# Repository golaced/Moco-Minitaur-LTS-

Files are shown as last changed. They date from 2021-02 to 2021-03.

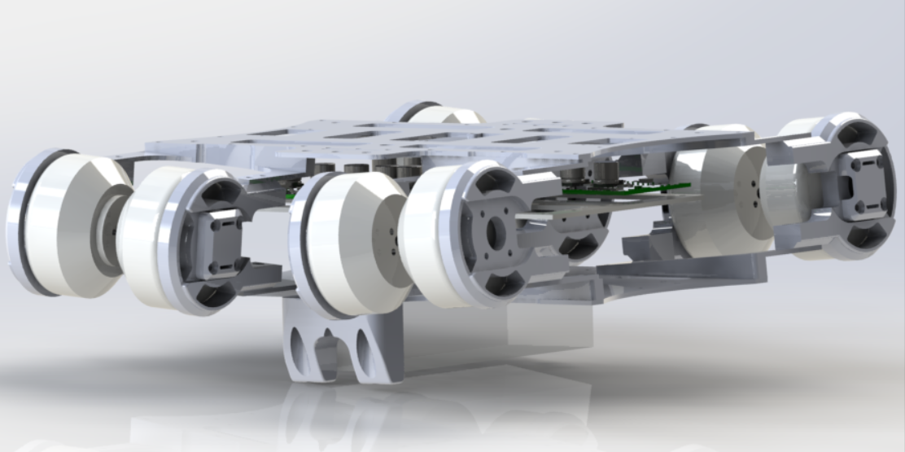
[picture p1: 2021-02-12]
教程4资料 机架设计/V2加工文件/渲染.PNG

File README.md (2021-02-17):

# Moco-Minitaur LTS 高性能 开源 力控 四足机器人 平台


本项目为开源桌面级8自由度四足机器人的相关资料，知乎教程文档：https://www.zhihu.com/column/c_1090923972006240256 </div><br>

教程1：Moco-ML项目介绍https://zhuanlan.zhihu.com/p/347235537</div><br>
教程2：机器人软硬件框架设计https://zhuanlan.zhihu.com/p/348091039</div><br>
教程3：电机驱动单元选https://zhuanlan.zhihu.com/p/349581111</div><br>
教程4：机器人主机架设计https://zhuanlan.zhihu.com/p/350553319</div><br>
教程5: ODrive驱动器改装https://zhuanlan.zhihu.com/p/351046678</div><br>
教程6：主控器设计和说明https://zhuanlan.zhihu.com/p/351052766</div><br>

官方taobao链接：https://item.taobao.com/item.htm?spm=a1z10.1-c.w4004-15110596499.22.6b86242c3mvjW9&id=589551490320
<br>
**-如果该项目对您有帮助请 Star 我们的项目-**<br>
**-如果您愿意分享对该项目的优化和改进请联系golaced@163.com或加入我们的QQ群567423074，加速开源项目的进度-**<br>

# 捐赠与项目后续开发计划<br>
____团队计划后期推出5kg~10kg级的足式机器人开发底盘，支持RPlidar激光雷达导航进行SLAM算法验证，能以相同的价格替代目前市面上同类的四轮小车平台如Autolabor等。
 
____如果您觉得该项目对您有帮助，也为了更好的项目推进和软硬件更新，如果愿意请通过微信捐赠该项目！


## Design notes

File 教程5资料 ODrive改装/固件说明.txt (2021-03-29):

V2 减小上电标定角度为45°
V3 增加硬件上锁飞车保护
V31 修复3.6无法驱动bug

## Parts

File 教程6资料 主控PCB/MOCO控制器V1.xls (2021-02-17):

Comment | Description | Designator | Footprint | Quantity
Header 2 | XH2.54 2P | BAT1 | HDR1X2 | 1 | 缺口朝向丝印
BEEP |  | BEEP? | DET402 | 1
Header 2 | 按键 | BOOT2 | 663*4*2.0/2.5mm | 1
0.1UF | 贴片电容 | C31, C38, C39, C41, C42, C44, C45, C46, C48, C49, C55, C60 | C 0402 | 12
1UF | 贴片电容 | C32 | C 0402 | 1
2.2UF | 贴片电容 | C33, C34 | C0603 | 2
10NF | 贴片电容 | C35 | C 0402 | 1
20PF | 贴片电容 | C36, C37 | C 0402 | 2
10uF | 贴片电容 | C40, C43 | C0603 | 2
0.1UF | 贴片电容 | C50, C51, C52 | C0603 | 3
100nF | 贴片电容 | C53 | C0603 | 1
Header 4 | PH2.0-4 | CAN5, CAN6, CAN7, CAN8, | PH2.0-4 | 5 | 缺口朝向丝印
BAT54WS | 单肖特基二极管 | D5 | SOD-323 | 1
PESD1CAN |  | D7, D8 | SOT-23 | 2
Header 3 | 2.54排针 | DCDC2,,PWM,P8 | HDR1X3 | 3
LED1 | LED 红蓝 | DS1, DS2 | SMDLED | 2
Header 4 | GH4P带锁端子 立 | IDLE2, RADIO1 | JST_GH_V4 | 2
LIS3MDL |  | LIS2 | LIS3MDL | 1
LSM6DS33 |  | LSM2 | LSM6DS33 | 1
S8050 | 8050/BCW846/BCW847 | Q3, Q4 | SOT-23R | 2
10K | 贴片电阻 | R34, R37, R39, R40 | R 0402 | 4
560R | 贴片电阻 | R41 | R 0402 | 1
1K | 贴片电阻 | R43 | R0603 | 1
10K | 贴片电阻 | R45 | R0603 | 1
100R | 贴片电阻 | R47, R48 | R 0402 | 2
120R | 贴片电阻 | R49, R54 | R0603 | 2
SPL06 |  | SPL2 | SPL06 | 1
Header 4 | SH立端子 | SWD2, USB_L2 | SH1.0-4P - up | 2
STM32F405RGT6 |  | U5 | LQFP64_M | 1
W25X16 | W25X16;SST25VF016;MX25L1605 | U6 | W25Q32FVZPIG | 1
TJA1050 |  | U7, U8 | SOP-8 | 2
RT9193-3.3/LP2985/SPX3819 | 降压IC | V2 | SOT23-5 | 1
8MHZ | 无源晶振 | X2 | PXCL | 1

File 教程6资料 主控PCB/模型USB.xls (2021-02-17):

Comment | Description | Designator | Footprint | LibRef | Quantity
USB-B(Mini) |  | USB | Micro_USB | USB5 | 1
USB-B(Mini) |  | USB1 | USB/SM0.8-6H5_M | USB5 | 1
Header 4 | 卧贴端子 | USB_L, USB_R | SH1.0-4P | Header 4 | 2

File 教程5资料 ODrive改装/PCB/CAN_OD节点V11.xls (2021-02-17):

Comment | Description | Designator | Footprint | Quantity
Header 2 | PH2.0-2 | BAT1 | PH2.0-2 | 1 | 缺口朝向丝印
Header 2 | 按键 | BOOT1, RST | 663*4*2.0/2.5mm | 2
2.2UF | 贴片电容 | C3, C4 | C0603 | 2
10NF | 贴片电容 | C5 | C 0402 | 1
20PF | 贴片电容 | C6, C7 | C 0402 | 2
0.1UF | 贴片电容 | C8, C9, C11, C12, C14, C15, C16, C17, C20 | C 0402 | 9
10uF | 贴片电容 | C10, C13 | C0603 | 2
Header 4 | PH2.0-4 | CAN1 | PH2.0-4 | 1 | 缺口朝向丝印
LED1 | LED蓝色 | DS1 | SMDLED | 1
10K | 贴片电阻 | R1, R4, R6 | R 0402 | 3
100R | 贴片电阻 | R10 | R 0402 | 1
120R | 贴片电阻 | R13 | R0603 | 1
Header 4 | SH1.0-4P 立 | SWD1, USB_L1 | SH1.0-4P - up | 2
STM32F405RGT6 |  | U1 | LQFP64_M | 1
TJA1050 |  | U4 | SOP-8 | 1
RT9193-3.3/LP2985/SPX3819 | 降压IC | V1 | SOT23-5 | 1
8MHZ | Crystal Oscillator | X1 | PXCL | 1

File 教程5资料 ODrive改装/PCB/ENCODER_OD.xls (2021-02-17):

Comment | Description | Designator | Footprint | LibRef | Quantity
Header 5 | GH立贴端子 | M0, M1 | GH1.25_5 | Header 5 | 2 | 配双头10cm线
Header 12 | Header, 12-Pin | P3, P4 | HDR1X12 | Header 12 | 2 | 不焊接 配排针

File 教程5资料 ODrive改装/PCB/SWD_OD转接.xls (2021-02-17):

Comment | Description | Designator | Footprint | LibRef | Quantity
10uF | Capacitor | C1, C4 | C0603 | CAP | 2
0.1uF | Capacitor, 普通电容 | C2, C3, C5 | C 0402 | CAP, Capacitor | 3
Header 6 | Header, 6-Pin | P1, P2 | HDR1X6 | Header 6 | 2 | 配排针不焊接
Header 4 | 立贴端子 | SWD1 | SH1.0-4P - up | Header 4 | 1 | 配双头5cm线
RT9193-3.3/LP2985/SPX3819 | 降压IC | V1 | SOT23-5 | RT9193-3.3/LP2985/SPX3819 | 1

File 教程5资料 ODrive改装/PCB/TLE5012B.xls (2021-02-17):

Comment | Description | Designator | Footprint | Quantity
100nF | Capacitor | C1 | C 0402 | 1
22nF | Capacitor | C2 | C 0402 | 1
LED1 | 蓝色LED | DS2 | SMDLED | 1
Header 5 | 卧贴端子 | P1, P2 | GH1.25_5 | 2 | 配双头异面20cm排线
470R | 0603 | R1 | R 0402 | 1
TLE5012B |  | U1 | SOP-8 | 1

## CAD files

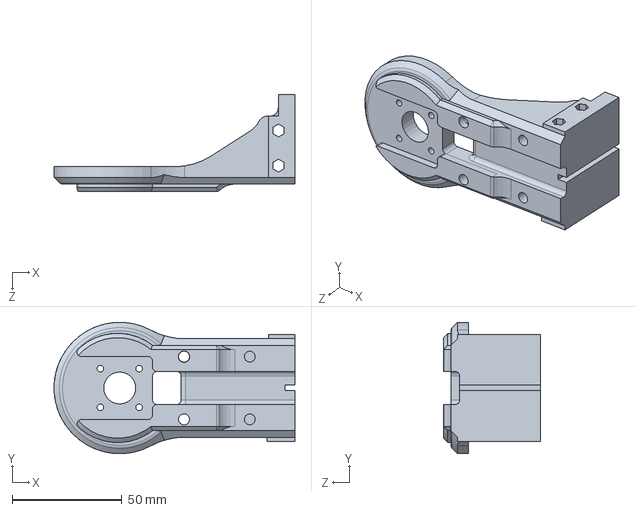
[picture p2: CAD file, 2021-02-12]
教程4资料 机架设计/V1工程文件/电机做1.SLDPRT
110.0 x 59.9 x 44.5 mm

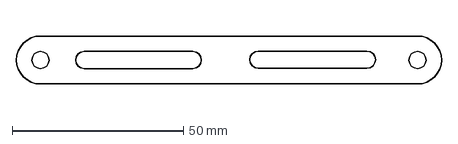
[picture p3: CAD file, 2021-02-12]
教程4资料 机架设计/V2加工文件/大腿1 3mm 4个.DXF
124.0 x 14.0 mm

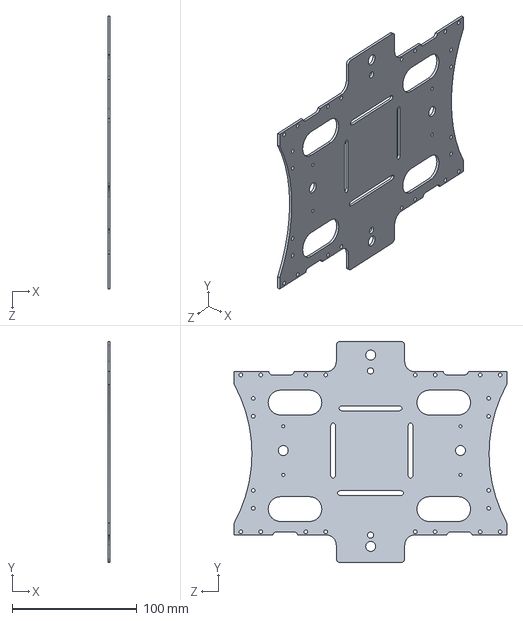
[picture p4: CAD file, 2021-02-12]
教程4资料 机架设计/V1工程文件/下盖.SLDPRT
2.00 x 177.5 x 219.0 mm

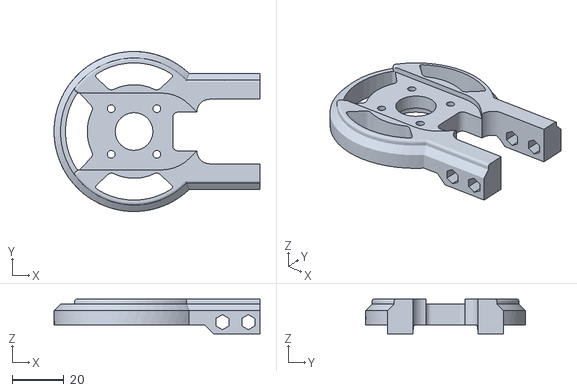
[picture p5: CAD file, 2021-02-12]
教程4资料 机架设计/V2加工文件/电机座 8个.STL
79.8 x 62.0 x 13.5

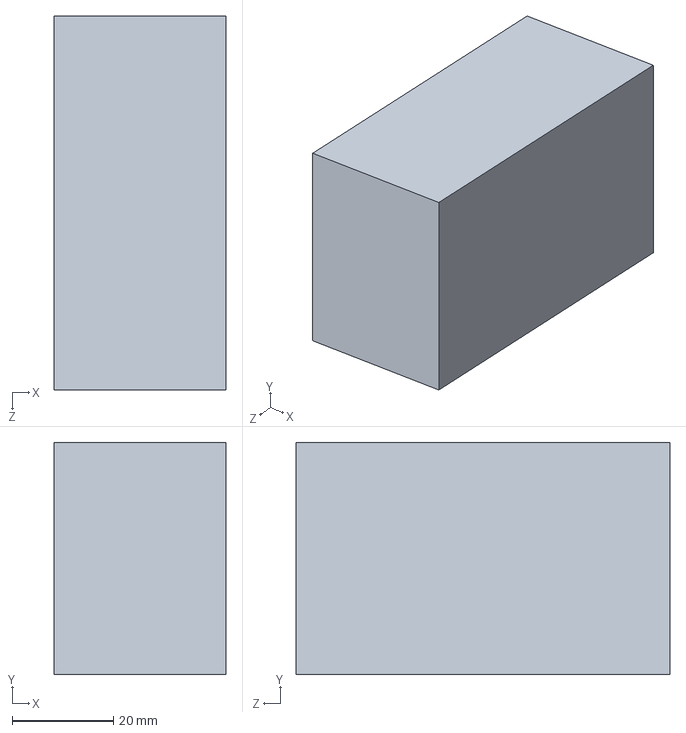
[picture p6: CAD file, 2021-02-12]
教程4资料 机架设计/V1工程文件/电池.SLDPRT
34.0 x 46.0 x 74.0 mm

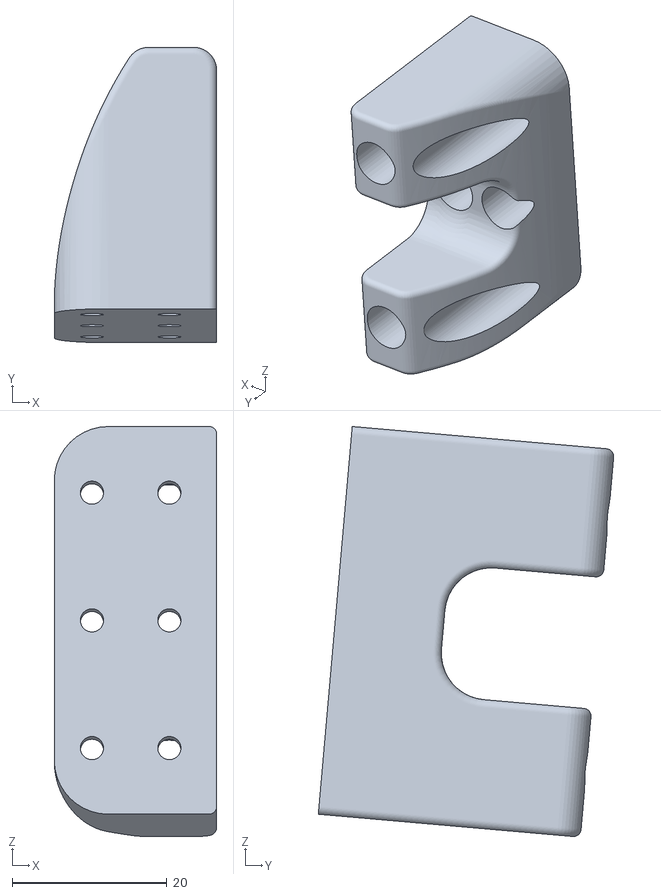
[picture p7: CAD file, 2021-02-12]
教程4资料 机架设计/V2加工文件/底盖支撑 2个.STL
21.0 x 38.2 x 53.0

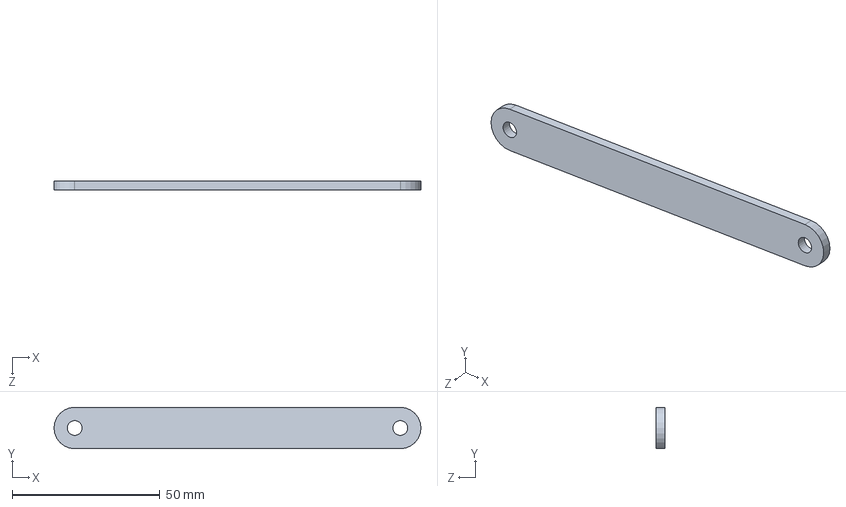
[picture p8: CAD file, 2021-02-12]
教程4资料 机架设计/V1工程文件/大腿1.SLDPRT
124.0 x 14.0 x 3.00 mm

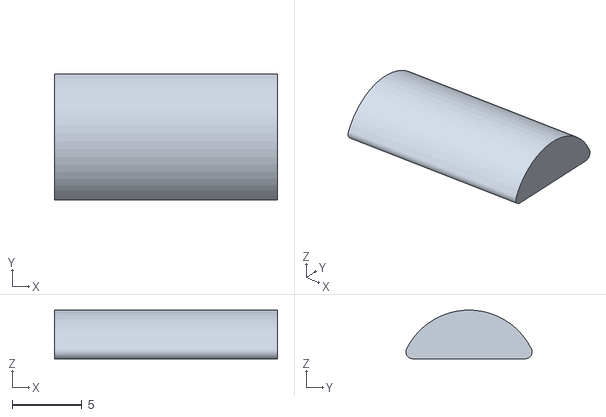
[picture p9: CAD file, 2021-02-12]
教程4资料 机架设计/V2加工文件/足底固定 8个.STL
16.0 x 9.06 x 3.49

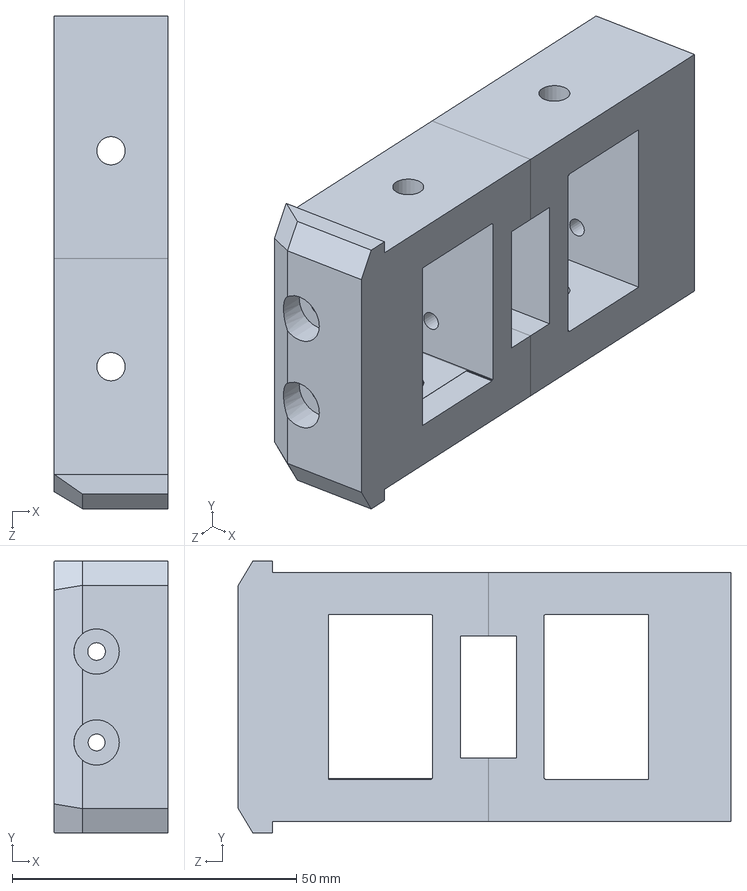
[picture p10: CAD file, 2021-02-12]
教程4资料 机架设计/V1工程文件/电机固定.SLDPRT
20.0 x 47.9 x 86.7 mm

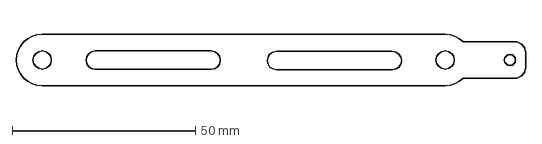
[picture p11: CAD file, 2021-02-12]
教程4资料 机架设计/V2加工文件/大腿2 3mm 4个.DXF
139.0 x 14.0 mm

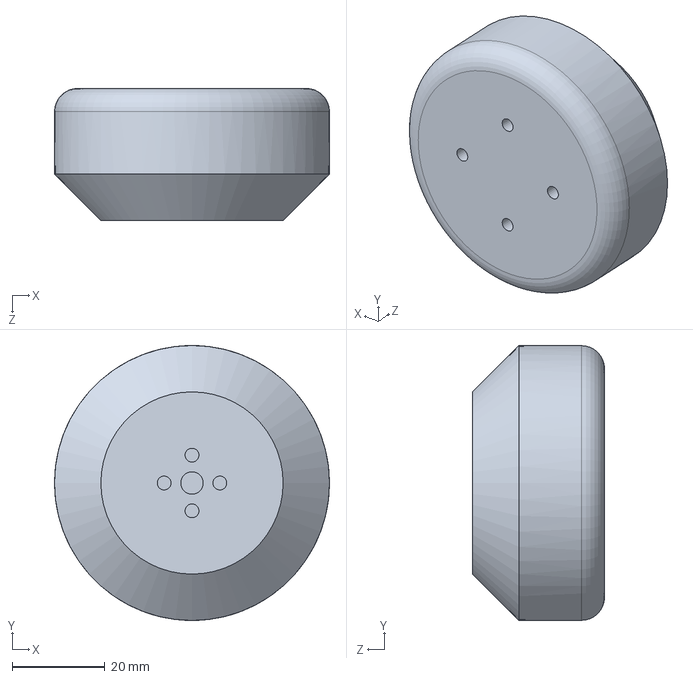
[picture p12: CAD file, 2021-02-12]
教程4资料 机架设计/V1工程文件/电机2.SLDPRT
59.3 x 59.3 x 28.5 mm

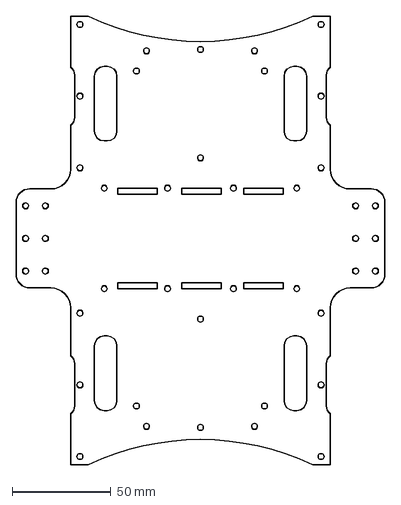
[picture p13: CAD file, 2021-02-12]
教程4资料 机架设计/V2加工文件/底盖 2mm.DXF
187.2 x 227.8 mm

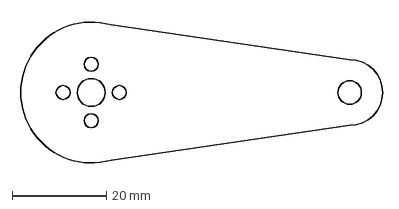
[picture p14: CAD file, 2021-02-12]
教程4资料 机架设计/V1工程文件/小腿 8个 3mm.DXF
77.9 x 32.4 mm

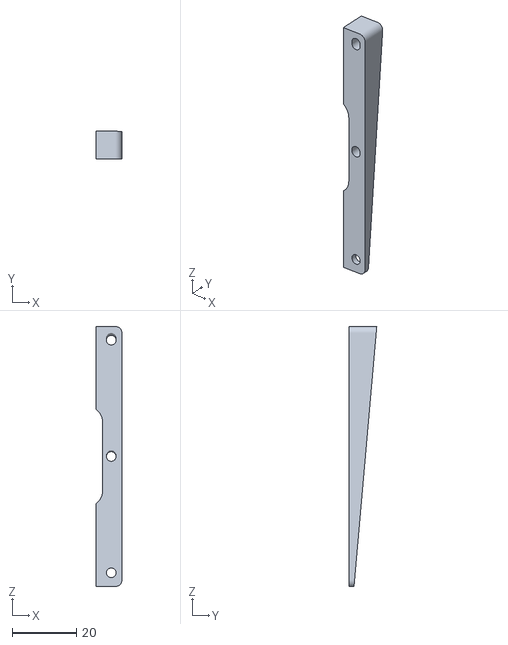
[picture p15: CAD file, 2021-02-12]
教程4资料 机架设计/V2加工文件/电机固定斜角 4个 镜像4个.STL
8.06 x 8.59 x 81.0

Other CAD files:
教程4资料 机架设计/V1工程文件/中间板子 1个 2.5mm.DXF
教程4资料 机架设计/V2加工文件/小腿 3mm 8个.DXF
教程4资料 机架设计/V1工程文件/小腿.SLDPRT
教程4资料 机架设计/V2加工文件/编码器保护 8个.STL
教程4资料 机架设计/V1工程文件/Odrive支撑.SLDPRT
教程4资料 机架设计/V1工程文件/Odrive支撑.STL
教程4资料 机架设计/V1工程文件/odrive.stp
教程4资料 机架设计/V1工程文件/上盖 1个 2mm.DXF
教程4资料 机架设计/V1工程文件/上盖.SLDPRT
教程4资料 机架设计/V1工程文件/下盖 1个 2mm.DXF
教程4资料 机架设计/V1工程文件/中间板子.SLDPRT
教程4资料 机架设计/V1工程文件/大腿1 8个 3mm.DXF
教程4资料 机架设计/V1工程文件/大腿2 8个 3mm.DXF
教程4资料 机架设计/V1工程文件/大腿2.SLDPRT
教程4资料 机架设计/V1工程文件/电机.SLDPRT
教程4资料 机架设计/V1工程文件/电机做1.STL
教程4资料 机架设计/V2加工文件/Odrive支撑 16个.STL
教程4资料 机架设计/V2加工文件/中间板子 2mm.DXF
教程4资料 机架设计/V2加工文件/电机固定 2mm 8个.DXF
教程4资料 机架设计/V2加工文件/顶盖 2mm.DXF

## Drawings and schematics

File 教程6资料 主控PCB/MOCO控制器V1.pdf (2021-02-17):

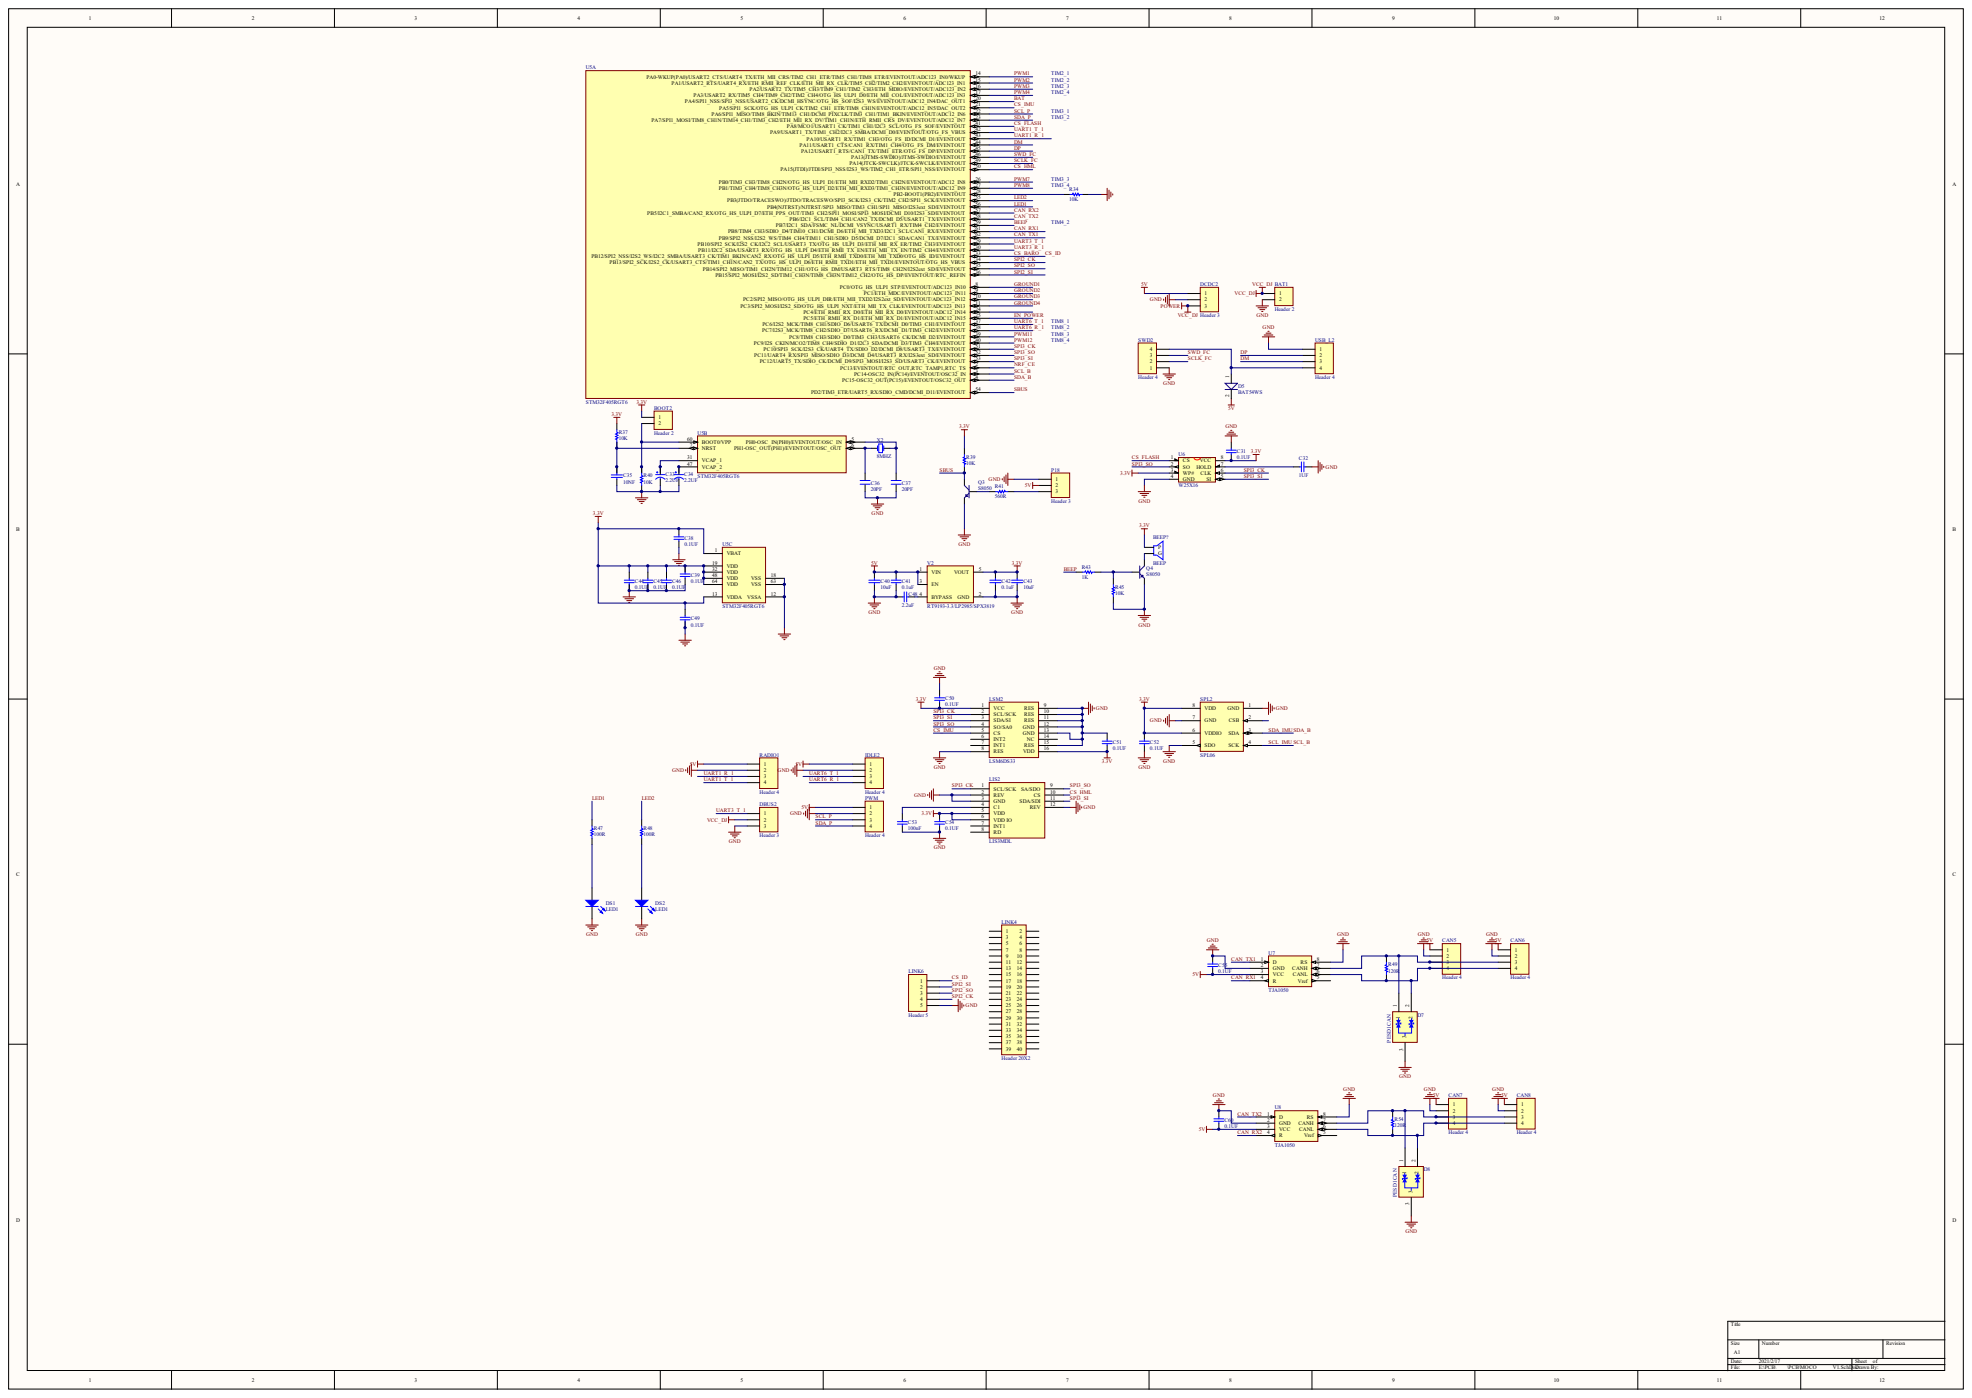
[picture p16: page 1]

BOOT0/VPP 60 NRST 7

VCAP_1 31

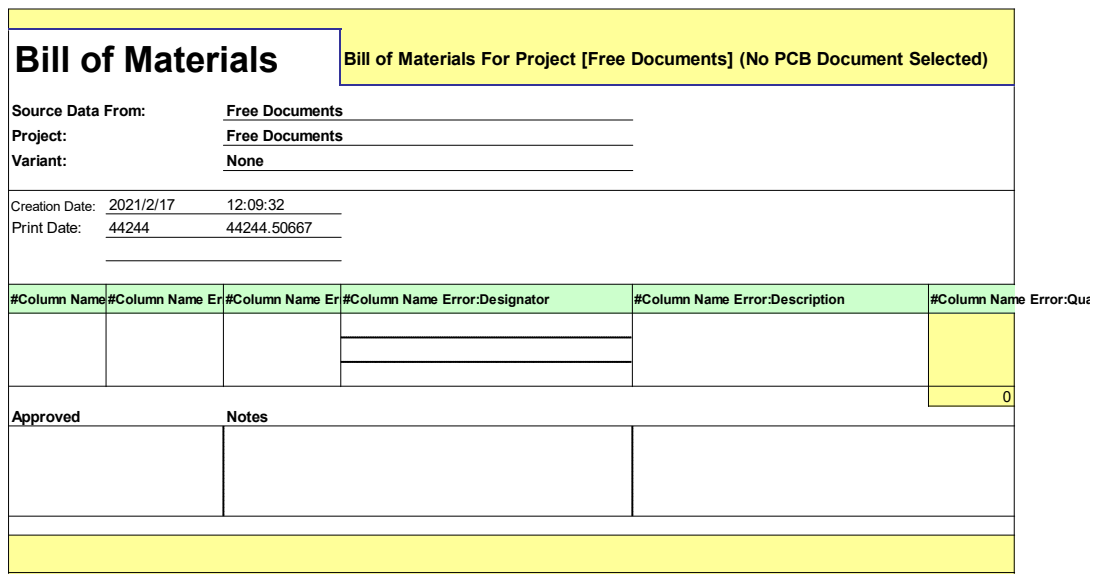
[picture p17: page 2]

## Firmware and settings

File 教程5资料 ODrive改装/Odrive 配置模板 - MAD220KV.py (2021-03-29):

#!/usr/bin/env python3
"""
Example usage of the ODrive python library to monitor and control ODrive devices
"""

from __future__ import print_function

import odrive
from odrive.enums import *
import time
import math
from fibre import Logger, Event
from odrive.utils import OperationAbortedException
from fibre.protocol import ChannelBrokenException
import sys

#-------------参数配置-------------
reset_all= 1 #擦除参数
en_index= False #使用索引
fast_per_cal = True #快速上电标定
en_brake_resistance= 0#使用功率电阻

gain_all = 0.15 #无命令下的位置闭环

gear_ratio = 1 #位置控制的减速比

pole = 14  #极对数
max_a= 25  #最大电流
r_max_a= 30 #最大电流采样
max_v= 36  #保护电压

cpr_all= 16384 #编码器CPR
calib_range = 0.15#标定误差冗余0.019999999552965164*10 RAD

vel_limit = 50000#turn/s 转速保护

def set_gains(odrv,axis):
    """
    Sets the nested PID gains to a good default
    """

    axis.controller.config.pos_gain = 100.0* gain_all#f [(counts/s) / counts] <<-------------无命令下的参数 CPR模式
    axis.controller.config.pos_gain = 0.01 * gain_all#f [(counts/s) / counts]
    axis.controller.config.vel_gain = 5.0 / 10000.0 * gain_all#[A/(counts/s)]
    axis.controller.config.vel_limit = vel_limit
    axis.controller.config.vel_integrator_gain = 0 * gain_all#[A/((counts/s) * s)]

    axis.controller.config.kp_theta = 0.04 *  6000 / (2 * math.pi)* gain_all#<<-------------考虑减速比的 360°位置闭环模式
    axis.controller.config.kd_theta = 5.0 / 10000.0 *  6000 / (2 * math.pi)* gain_all
    axis.controller.config.kp_gamma = 0.0 *  6000 / (2 * math.pi)* gain_all
    axis.controller.config.kd_gamma = 5.0 / 10000.0 *  6000 / (2 * math.pi)* gain_all

def calibrate_motor(odrv, axis):
    # time.sleep(0.5)
    print('Calibrating motor...',end='',flush=True)
    run_state(axis, AXIS_STATE_MOTOR_CALIBRATION, True)
    axis.motor.config.pre_calibrated = True# then set motor pre calibrated to true
    print('Done');

def calibrate_motor_and_zencoder(odrv,axis):
    """
    Runs motor and encoder calibration (with z index) and saves
    Enables closed loop control on startup and encoder search on startup
    """

    calibrate_motor(odrv, axis)

    print('Calibrating encoder...',end='',flush=True)
    axis.encoder.config.use_index = True
    run_state(axis, AXIS_STATE_ENCODER_INDEX_SEARCH, True)
    run_state(axis, AXIS_STATE_ENCODER_OFFSET_CALIBRATION, True)
    axis.encoder.config.pre_calibrated = True
    print('Done');

    print('Setting startup flags...',end='',flush=True)
    # axis.config.startup_encoder_index_search = True
    axis.config.startup_encoder_index_search = True
    axis.config.startup_closed_loop_control = True
    print('Done with axis.')

def run_state(axis, requested_state, wait):
    """
    Sets the requested state on the given axis. If wait is True, the method
    will block until the state goes back to idle.

    Returns whether the odrive went back to idle in the given timeout period,
    which is 10s by default.
    """
    axis.requested_state = requested_state
    timeout_ctr = 100; # 20s timeout for encoder calibration to finish
    if wait:
        while(timeout_ctr > 0): # waits until state goes back to idle to continue
            time.sleep(0.2)
            timeout_ctr -= 1
            if axis.current_state == AXIS_STATE_IDLE:
                break
    return timeout_ctr > 0

def reboot_odrive(odrv):
    """
    Reboot odrive
    """
    try:
        odrv.reboot()
    except ChannelBrokenException:
        print('Lost connection because of reboot...')

def reset_odrive(odrv):
    """
    Erase config
    """
    print('Erasing config and rebooting...')
    odrv.erase_configuration()
    reboot_odrive(odrv)

def init_odrive(odrv):
    """
    NOTE: does not save
    """
    print('Initializing ODrive...')
    odrv.config.brake_resistance = 2.0*en_brake_resistance# 配置功率耗散电阻阻值，我们使用的的功率耗散电阻阻值为 2 Ohm

    odrv.axis0.motor.config.pole_pairs = pole
    odrv.axis1.motor.config.pole_pairs = pole

    odrv.axis0.motor.config.resistance_calib_max_voltage = 4.0#配置电机参数校准时的电压，当电机的相电阻越高此值应该越高，但是如果此值过高会造成电流过大，产生过流保护错误
    odrv.axis1.motor.config.resistance_calib_max_voltage = 4.0#配置电机参数校准时的电压，当电机的相电阻越高此值应该越高，但是如果此值过高会造成电流过大，产生过流保护错误

    odrv.axis0.encoder.config.cpr = cpr_all#16384
    odrv.axis1.encoder.config.cpr = cpr_all#16384

    #odrv.axis0.encoder.config.bandwidth = 3000#设置编码器 PLL 带宽，一般对于高分辨率编码器 (> 4000个计数/转) 此值应该越高，这样有助于减少电机振动
    #odrv.axis1.encoder.config.bandwidth = 3000#设置编码器 PLL 带宽，一般对于高分辨率编码器 (> 4000个计数/转) 此值应该越高，这样有助于减少电机振动
    #[RW] odrv0.axis0.encoder.config.calib_range calib_range = 0.019999999552965164 (float)
#类型为 [float]，通过编码器cpr检查所需的精度，用于在执行编码器偏移校准时编码器的实际输出计算的移动距离和电机开环步进移动距离之间允许的最大误差，超过此误差将报错 ERROR_CPR_OUT_OF_RANGE。

#[RW] odrv0.axis0.encoder.config.calib_scan_distance
#类型为 [float]，单位为 [rad]，编码器偏移校准时转动的距离，此值越大校准精度相对越高，但是同时校准所需的时间越长。
    #odrv.axis0.config.watchdog_timeout = 3
    #odrv.axis1.config.watchdog_timeout = 3
    odrv.config.dc_bus_overvoltage_trip_level = max_v

    odrv.axis0.motor.config.current_lim = max_a #40
    odrv.axis1.motor.config.current_lim = max_a #40
    #odrv.config.dc_max_positive_curren  = max_a
    odrv.axis0.motor.config.requested_current_range = r_max_a
    odrv.axis1.motor.config.requested_current_range = r_max_a
    
    odrv.axis0.controller.config.vel_limit = vel_limit
    odrv.axis1.controller.config.vel_limit = vel_limit

   # odrv.axis0.motor.current_control_.max_allowed_current
    # odrv.axis0.config.calibration_lockin.current = 10
    # odrv.axis0.config.calibration_lockin.ramp_time = 0.4
    # odrv.axis0.config.calibration_lockin.ramp_distance = 3.1415927410125732
    # odrv.axis0.config.calibration_lockin.accel = 20
    # odrv.axis0.config.calibration_lockin.vel = 40
    # odrv.axis1.config.calibration_lockin.current = 10
    # odrv.axis1.config.calibration_lockin.ramp_time = 0.4
    # odrv.axis1.config.calibration_lockin.ramp_distance = 3.1415927410125732
    # odrv.axis1.config.calibration_lockin.accel = 20
    # odrv.axis1.config.calibration_lockin.vel = 40
    odrv.axis0.controller.config.gear_ratio = gear_ratio
    odrv.axis1.controller.config.gear_ratio = gear_ratio
    
    odrv.axis0.motor.config.calibration_current = 10
    odrv.axis1.motor.config.calibration_current = 10

    odrv.axis0.motor.config.pre_calibrated = fast_per_cal
    odrv.axis1.motor.config.pre_calibrated = fast_per_cal

    odrv.axis0.encoder.config.pre_calibrated = True #HALL 传感器下直接跳过标定 使用存储偏差 
    odrv.axis1.encoder.config.pre_calibrated = True #HALL 传感器下直接跳过标定 使用存储偏差 
    print('Done!!!!!!!!!!!!!!!!!!!!')

def set_odrive_limits(odrv,axis,cur_lim):
    """
    Set motor current limits
    """
    axis.motor.config.current_lim = cur_lim

def calibrate_odrive(odrv):
    """
    Calibrate motors and encoders (including index) on both axes
    """
    print('Calibrating axes...')

    calibrate_motor_and_zencoder(odrv,odrv.axis0)
    calibrate_motor_and_zencoder(odrv,odrv.axis1)
    print('Done.')
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

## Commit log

2021-02-12 更新机架
    [Odrive支撑 16个.STL, Odrive支撑.SLDPRT, Odrive支撑.STL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]
2021-02-17 更新教程
    [CAN_OD节点V11.PcbDoc, CAN_OD节点V11.xls, ENCODER_OD.xls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]
2021-03-29 更新驱动
